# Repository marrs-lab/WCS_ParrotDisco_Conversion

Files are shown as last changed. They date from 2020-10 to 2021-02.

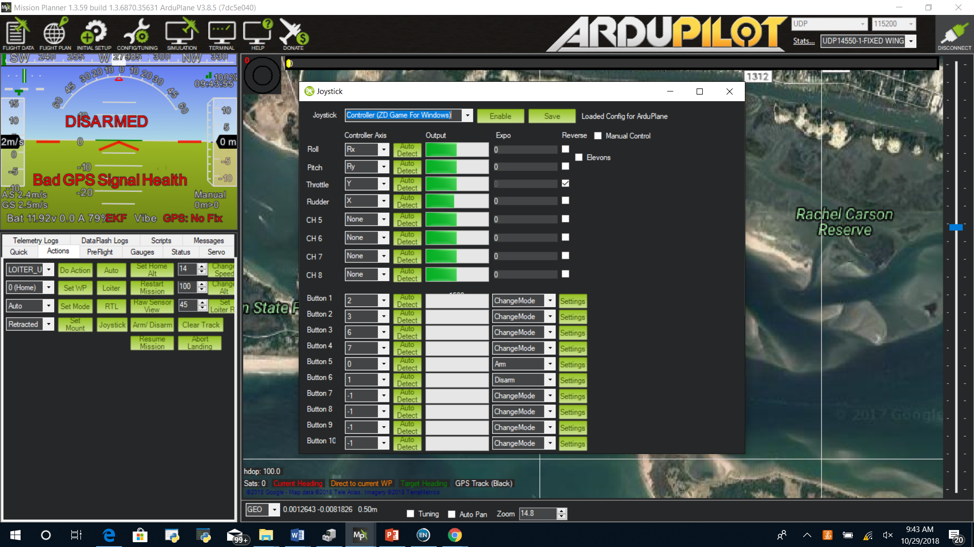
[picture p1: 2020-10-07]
Notes/Gamepad settings .png

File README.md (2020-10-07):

# WCS_ParrotDisco_Conversion

Before we begin, there are some important warnings…

**WARNING** 
Modifying the Parot Disco will void any warranties and could damage the aircraft. Only perform these modifications if you have adequate technical skills to 
perform the modifications.

**Disclaimer** 
The information provided by [Julian Dale or Duke University MaRRS Lab] (“we,” “us” or “our”) on [marineuas.net or Github/marrs-lab] (the “Site”) is for general informational purposes only. All information on the Site is provided in good faith, however we make no representation or warranty of any kind, express or implied, regarding the accuracy, adequacy, validity, reliability, availability or completeness of any information on the Site.

Under no circumstance shall we have any liability to you for any loss or damage of any kind incurred as a result of the use of the site or reliance on any information provided on the site. Your use of the site and your reliance on any information on the site is solely at your own risk. 

About the information included:

>

There are three folders containing ;

| Folder | Description |
| --- | --- |
| 3D Printer Files | STL's for printing the mouting frame |
| Autopilot files | The files required to transfer to the Parot Disco CHUCK autopilot to enable running Arduplane and on the autopilot for aircraft and external camera control and the parameters to set the aircraft up. |
| Manual | Manual for operating the aircraft and flight planning. Initial set up, calibrating sensors and installing Sony gamepad. Using external WiFi for extended range. Also notes on camera set up and modifying the parameters file for camera control using seagulUAV #MAP2 camera trigger |
| Notes | Information for converting the Disco to carry and trigger the Sony RX0 camera. Also manufacturing a 7000mAhr LiIon battery pack |
| QGroundControl | Links to most recent tested version of QGroundControl |

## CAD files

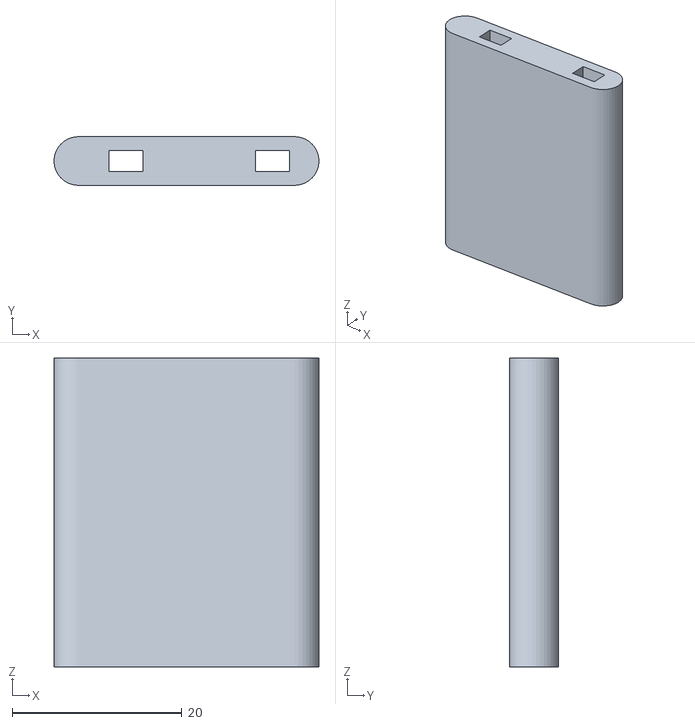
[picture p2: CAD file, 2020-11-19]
3D printer files/Dummy RX0 battery case v5.0.STL
31.2 x 5.75 x 36.4

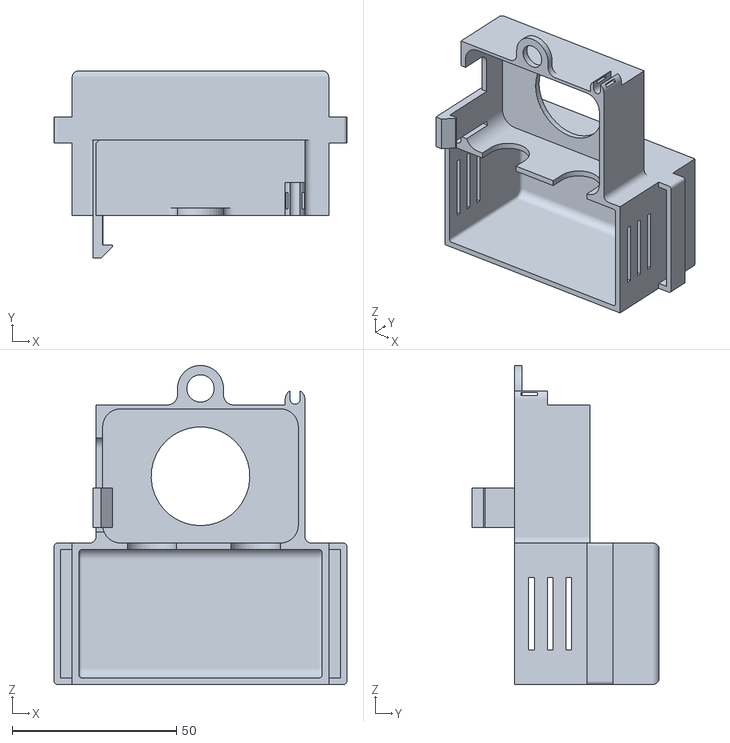
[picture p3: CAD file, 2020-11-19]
3D printer files/Disco RX0 mountv4.2STL.STL
89.0 x 57.0 x 97.0

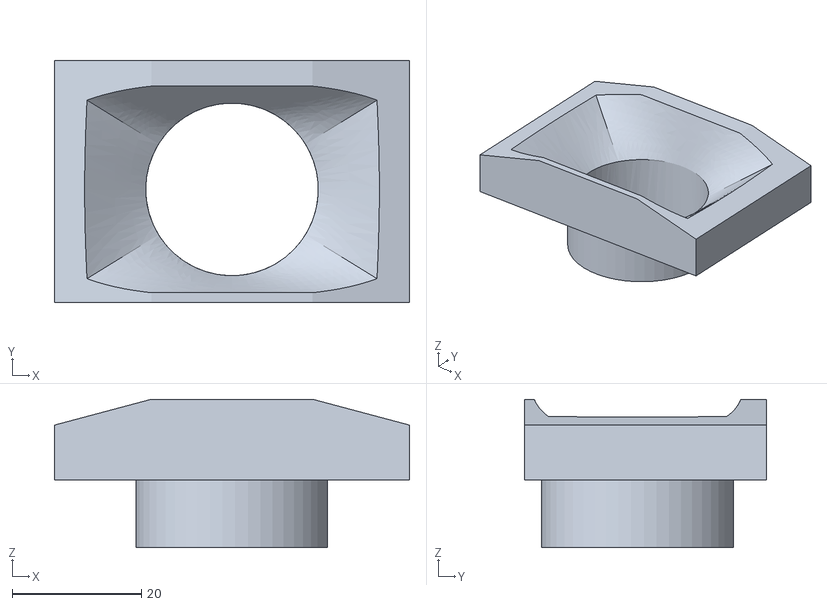
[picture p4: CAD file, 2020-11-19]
3D printer files/RX0 lens shield v2.0.STL
55.0 x 37.5 x 23.0

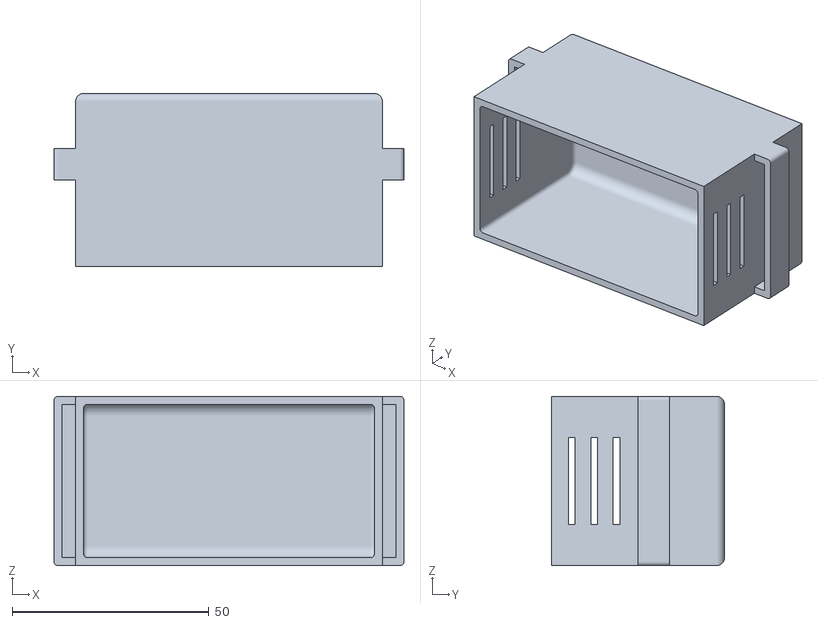
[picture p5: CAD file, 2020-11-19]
3D printer files/Disco 7000mahr battery tray.STL
89.0 x 44.0 x 43.0

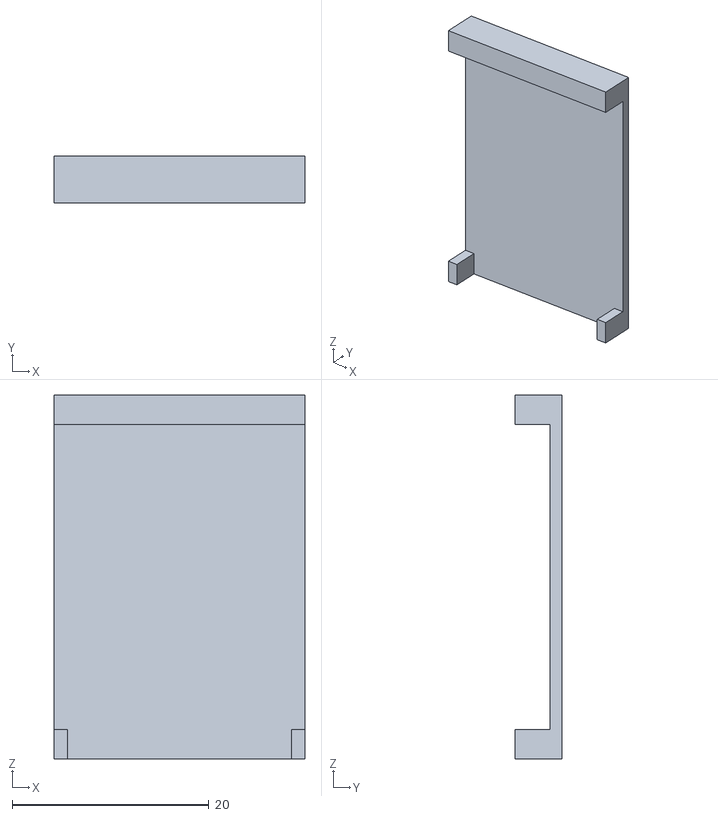
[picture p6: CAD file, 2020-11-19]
3D printer files/Dummy battery coverv2.0.STL
25.5 x 4.75 x 37.0

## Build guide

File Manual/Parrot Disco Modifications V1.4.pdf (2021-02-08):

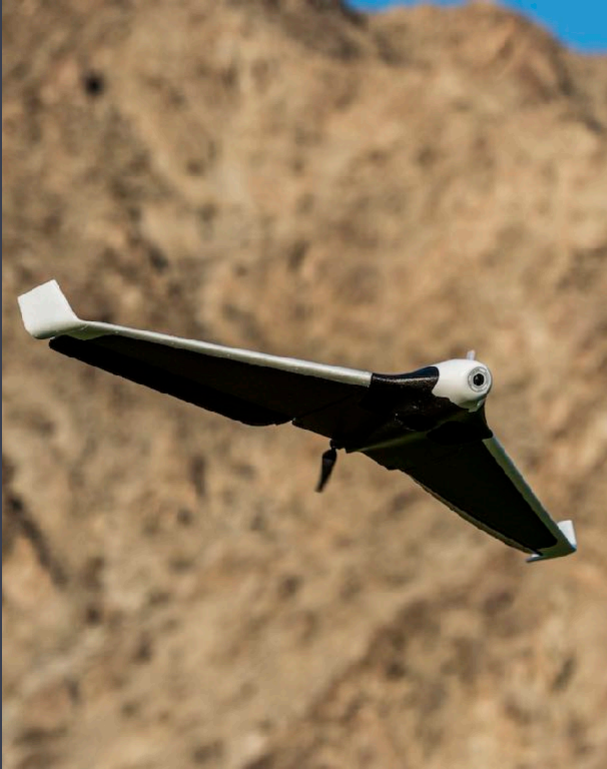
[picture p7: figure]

# Julian Dale

# THE PARROT DISCO

# MODIFIED

### Flight manual for conversion and operation

Version 1.4. 2021-02

## Background to the

# Modifications

- Load arduplane firmware on aircraft to allow flight planning capability
- Install downward facing RGB camera for mapping
- Setup PS4 wireless remote controller for manual flight
- Define parameters and mission planning protocols under
QGroundcontrol environment
- Provide data process to import images into Pix4D for analysis.

Although the Parrot disco is a very capable, easy to fly and inexpensive aircraft, it lacks the ability to fly mapping missions under the parrot Freeflight app environment. To be fair this aircraft was never initially intended for this type of operation. Parrot did however provide the architecture to allow the disco to fly under the open source ardupilot firmware.

The origins of this project were to create a very low cost mapping aircraft with extended flight time. The intent was to send this out to field teams within the WCS (Wildlife Conservation Society) network to provide them with mapping and inspection capabilities in order to help their conservation efforts.

# Overview

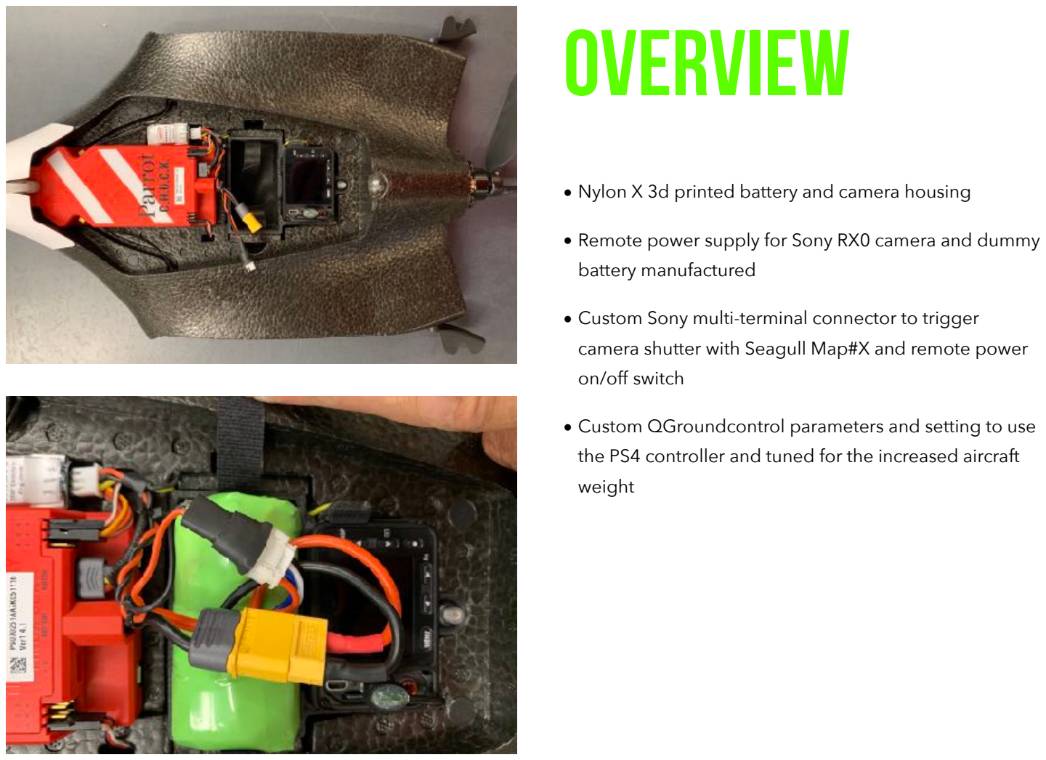
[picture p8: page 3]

- Nylon X 3d printed battery and camera housing
- Remote power supply for Sony RX0 camera and dummy battery manufactured
- Custom Sony multi-terminal connector to trigger camera shutter with Seagull Map#X and remote power on/off switch
- Custom QGroundcontrol parameters and setting to use the PS4 controller and tuned for the increased aircraft weight

# Contents

## 1. Installing the PS4 controller 2. Connecting the Disco 3. Configuring QGroundcontrol 4. Camera setup 5. Flight planning 6. Flight execution 7. Post flight data management 8. Maintenance

## Appendix A. Installing arduplane B. Load parameter file C. Camera specifications D. Airframe modifications E. Checklists: Pre-fight/maintenance F. Notes

# 1. Install PS4 controller

## DualShock 4 Bluetooth Pairing Settings

Step 1:
- To pair the DS4 with a computer, first put the controller into pairing mode by press and HOLDING the PlayStation button and Share button at the same time for 3 seconds. Hold these buttons until the light bar starts rapidly flashing.
Step 2:
- If your Operating System is Windows 7 then you have to right click on the Bluetooth Icon on the bottom right tray. If you are using Windows 8 or higher, open Bluetooth Settings by clicking on the Speech Bubble icon in the Task Bar on the bottom right corner.
- This will launch Action Center, click on Bluetooth and wait for the Wireless Controller to Appear.
- Click on it and type 0000 for typing the Pair Code.

That’s it, the controller is now connected wirelessly. In case you find issue with detecting the Wireless Controller after turning on Bluetooth, troubleshoot your PC Bluetooth adapter by updating drivers.

## USB Connection

- The controller can also be connected directly to the PC with a USB to USB micro cable. This plugs into the charge port on the front of the controller.

## Power up Disco

1. Install battery as shown.
2. Connect main battery lead (Yellow XT60 connector)
3. Press power button once (Pitot tube). Aircraft will start up. Wait for the long tone
4. Press power button 3 times in quick succession. This will boot the Disco into Arduplane and it will play a short tune as it boots up.

## WiFi connection

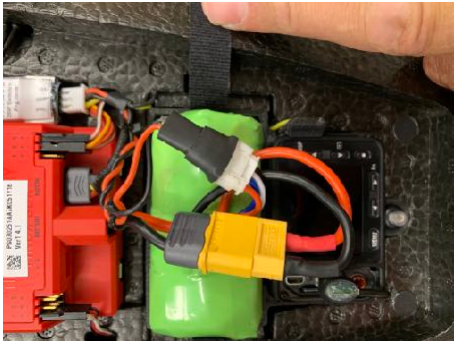
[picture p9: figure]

1. Use a long range USB WiFI modem such as the Alfa Long-Range Dual-Band AC1200 Wireless USB 3.0 Wi-Fi Adapter w/2x 5dBi External Antennas. You may need to download the latest driver for the Alfa USB WiFi modem here https://www.alfa.com.tw/download/all/1.htm (https://www.alfa.com.tw/download/all/1.htm)
2. Connect USB WiFi modem to the computer
3. Go to computer device manager and disable the computers inbuilt network adaptor or turn off the internal WiFi. *ensure you are only connecting to the aircraft using the long range WiFi modem and not your computers internal WiFi*
3. Connect to Disco WiFi from the computers network connection using the USB modem. Disco should appear as a DISCO-xxxxx as a WiFi connection **It is highly advised to disable all “connect automatically” options for your other WiFi connections. You do not want the aircraft to disconnect mid flight and have your computer connect to another network.**
4. Open QGroundcontrol. The Disco should connect automatically after a few seconds. If you encounter any issues. Shut down QGroundcontrol, ensure the disco is booted into Arduplane (three button presses on the pitot), the WiFi is connected to the aircraft then restart the app.

# 2. Connecting Disco

Getting QGroundControl up and running is quick and easy:
1. Download and install (https://docs.qgroundcontrol.com/en/getting_started/download_and_install.html) the application. Current stable version tested with the modified Disco is V4.0.10. Other versions many not function properly. You can go the the GitHub site to download previous versions. The link is on the downloads page for qGroungcontrol.
2. Start QGroundControl.
3. Attach your vehicle to the ground station device via USB, through a telemetry radio, or over WiFi. QGroundControl should detect your vehicle and connect to it automatically.
That's it! If the vehicle is ready to fly, QGroundControl should display Fly View (https://docs.qgroundcontrol.com/en/FlyView/FlyView.html) as shown below (otherwise it will open Setup View). (https://docs.qgroundcontrol.com/en/SetupView/SetupView.html)

# 3. Configuring QGroundcontrol

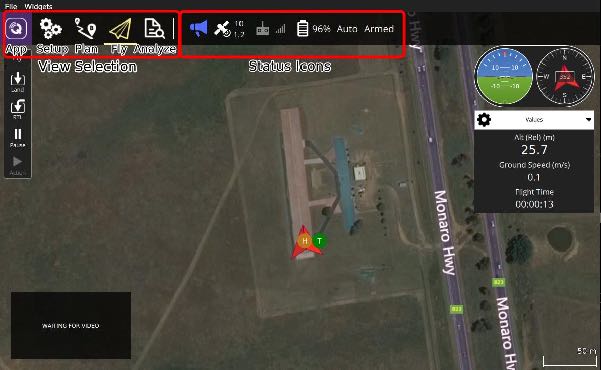
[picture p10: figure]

A good way to become familiar with QGroundControl is to start experimenting:

- Use the toolbar (https://docs.qgroundcontrol.com/en/toolbar/toolbar.html) to switch between the main views:
- Settings: (https://docs.qgroundcontrol.com/en/SettingsView/SettingsView.html) Configure the QGroundControl application.
- Setup: (https://docs.qgroundcontrol.com/en/SetupView/SetupView.html) Configure and tune your vehicle.
- Plan: (https://docs.qgroundcontrol.com/en/PlanView/PlanView.html) Create autonomous missions.
- Fly: (https://docs.qgroundcontrol.com/en/FlyView/FlyView.html) Monitor your vehicle(s) while flying.
- Click the Status icons on the toolbar to find out the status of the connected vehicle. While the UI is fairly intuitive, this documentation can also be referenced to find out more.

## Controller calibration

To configure a joystick:

1. Start QGroundControl and connect to a vehicle.
2. Connect the Joystick or Gamepad to a USB port or bluetooth.
3. Select the Gear icon (Vehicle Setup) in the top toolbar and then Joystick in the sidebar. The screen below will appear.
4. Make sure your joystick is selected in the Active joystick dropdown.
5. Press the Calibrate button and then follow the on-screen instructions to calibrate/move the sticks.
6. Test the buttons and sticks work as intended by pressing them, and viewing the result in the Axis/Button monitor.
7. Select the flight modes/vehicle functions activated by each joystick button. A maximum of 16 joystick button actions can be set.
8. Check the Enable joystick input checkbox to begin sending joystick commands to the vehicle.

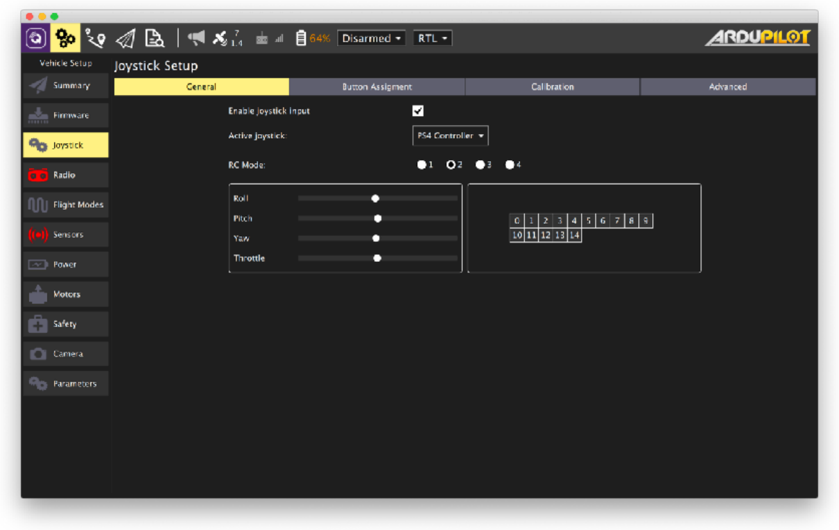
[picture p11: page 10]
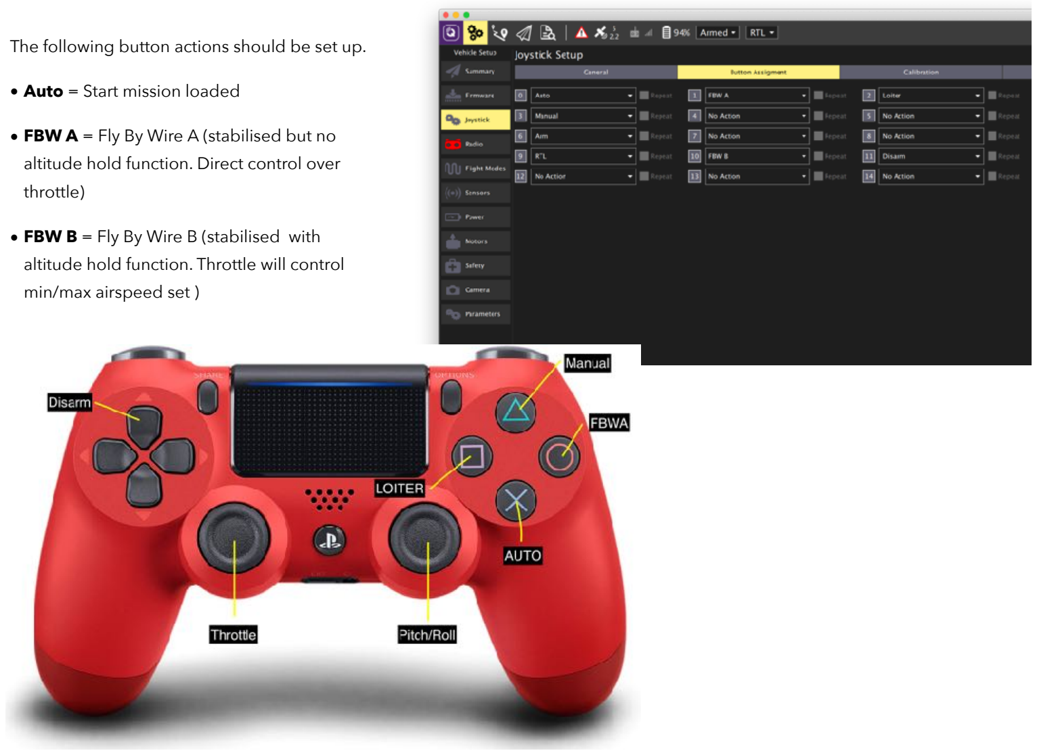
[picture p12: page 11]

The following button actions should be set up.

- Auto = Start mission loaded
- FBW A = Fly By Wire A (stabilised but no altitude hold function. Direct control over throttle)
- FBW B = Fly By Wire B (stabilised with altitude hold function. Throttle will control min/max airspeed set )

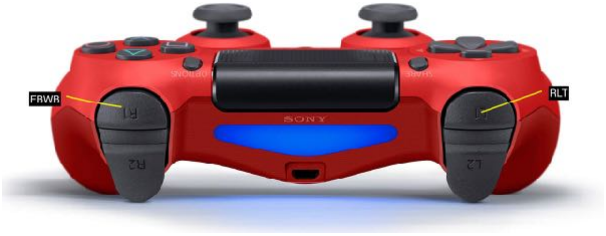
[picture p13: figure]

- Loiter = Will put aircraft into an orbit and maintain altitude
- Manual = Full manual control. NOT RECOMMENDED FOR FLIGHT. Use this mode only to verify flight controls on the ground.
- Arm = Arm the motor ready for takeoff
- Disarm = Disarm the motor
- RTL = Return to Launch. Aircraft will return to the home position and orbit.

## Sensor calibration

Perform the following calibrations as instructed

- Accelerometer
- Compass - Note. Ensure the battery cowling is fitted during compass calibration.
- Level Horizon = Using the level bubble measure on your phone. Sit the phone on the autopilot and lift the nose up by 3deg by placing something under the airframe. Ensure the wings are horizontal. When the aircraft is in the correct position and is completely still, hit the “level horizon” button
- Cal Baro/Airspeed = Cover the pitot tube with your had so it measure the static air pressure and is not influenced by the wind.

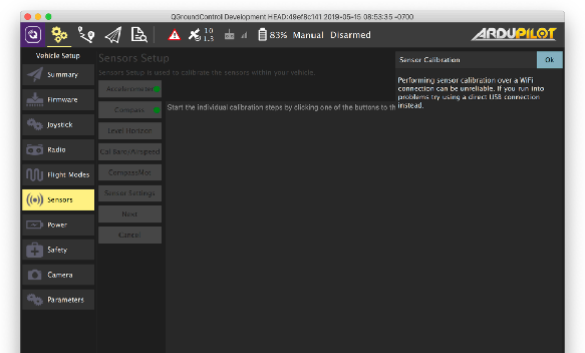
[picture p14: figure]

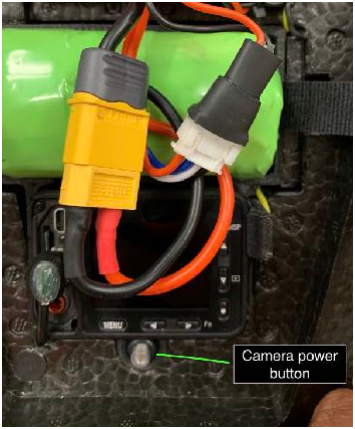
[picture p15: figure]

## Camera settings

Install the micro SD card.

Plug in the Sony Multi connector to the camera.

With the camera connected to the main flight battery, press the button below the camera to turn the camera on

A new or unformatted SD card will require a database to be set up before use. Power up the camera and hit “enter” at the image database creation prompt.

It is important to set the following camera parameters

1. Aspect ratio = 4:3
2. Manual shutter speed = 1/1250 is a good default speed
3. ISO = Auto
4. Focus = Wide
5. Set the camera time to GMT
6. Ensure the SD card has enough space

# 4. Camera setup

## Camera Parameters

| Width | Height
Sensor Size | 13.2mm | 8.8mm
Image px | 4272 | 3200
Focal length | 7.7mm

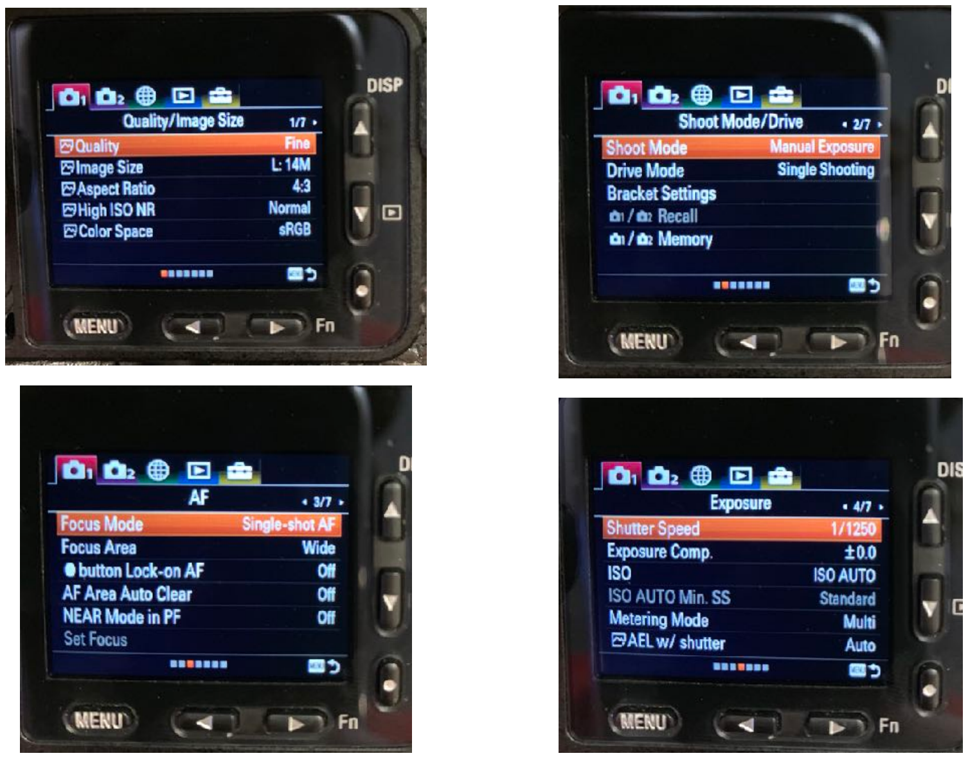
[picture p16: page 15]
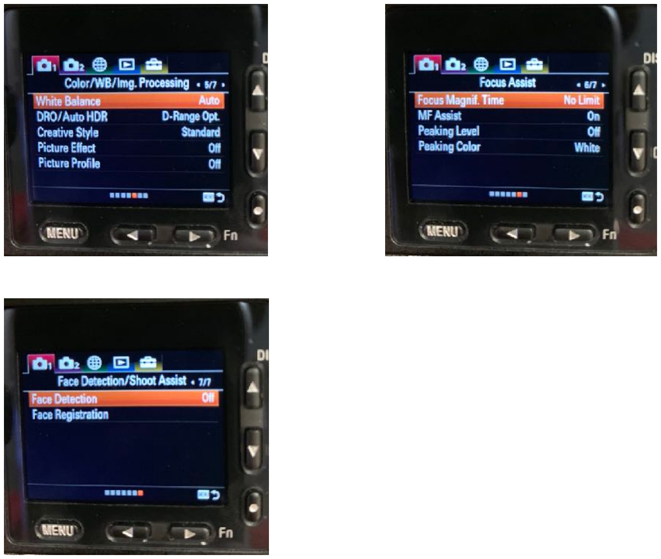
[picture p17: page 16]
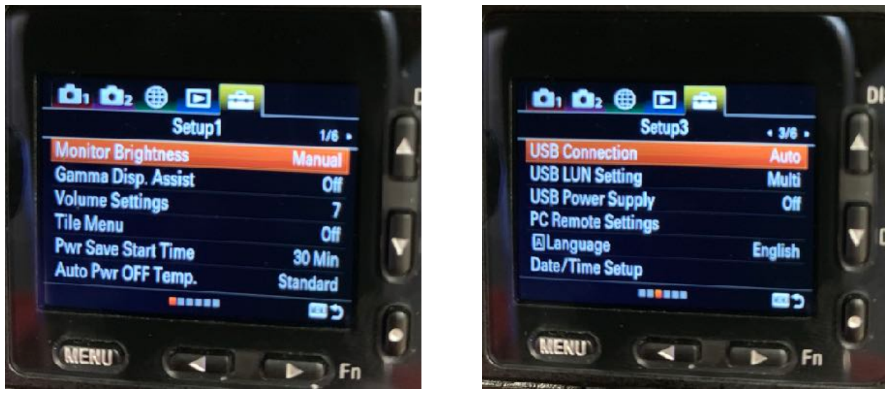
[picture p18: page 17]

# 5. Flight planning

## 1. Download base maps

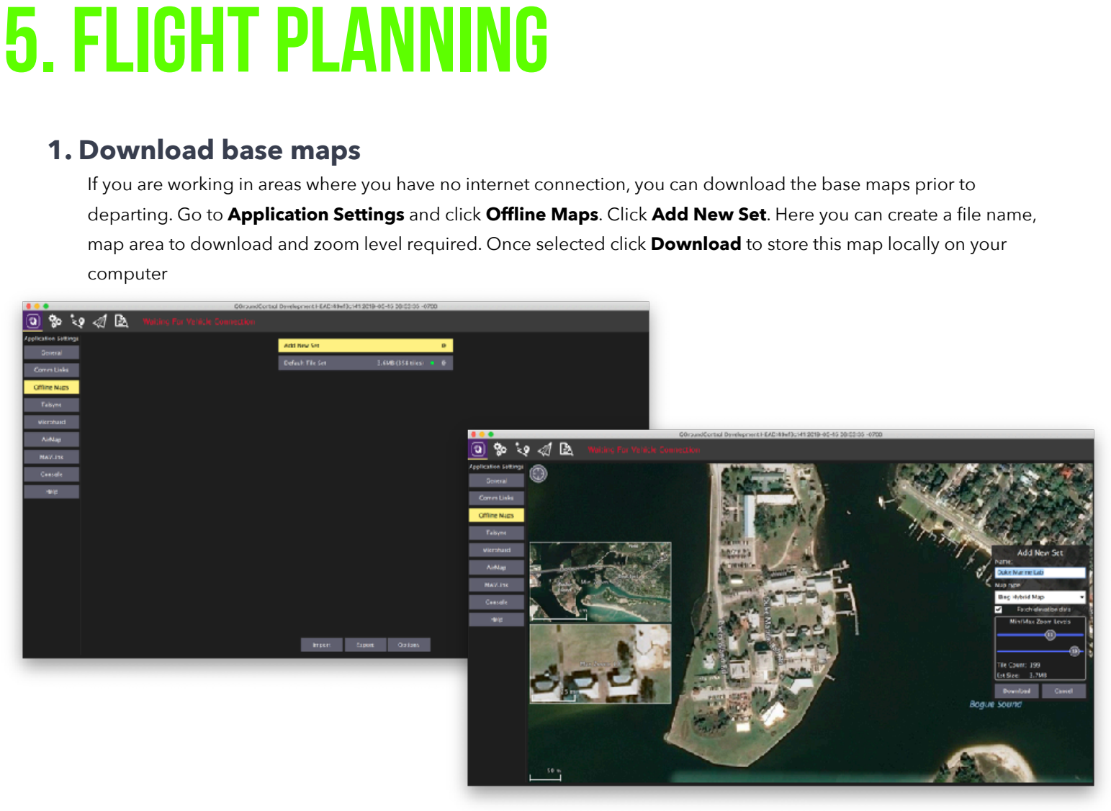
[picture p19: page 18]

If you are working in areas where you have no internet connection, you can download the base maps prior to departing. Go to Application Settings and click Offline Maps. Click Add New Set. Here you can create a file name, map area to download and zoom level required. Once selected click Download to store this map locally on your computer

## 2.Planning a Survey

1. Home position will be set automatically at the position the Disco is powered up.
2. Click on Takeoff and move the waypoint close to the takeoff location and at an altitude where it will clear all obstacles.
3. The takeoff parameters will automatically be set in position1 of the mission list. Set the altitude to a sufficient height to clear all obstacles at takeoff. Set the takeoff pitch angle to 25deg
4. Set a waypoint close to the takeoff and in a position where the aircraft has a good entry to the first survey waypoint. You may need to adjust the current set survey speed if the winds are strong. To change this you need to click the “gear” icon and then select the parameters tab. In the search window type “trim_arspd_cm” Set speed to 1500cm/s for light winds. 1700cm/s for moderate and 1900cm/s for strong winds ~18mph. This will be the survey flight speed used during the flight.
5. Set a Survey area up as desired. Additional grips around the polygon can be added by clicking on the + on the perimeter. Set the camera to the Sony RX0.
6. Select the desired GSD or Altitude , Overlap (70% is a safe default for mapping). Adjust the orientation as required for efficiency. In winds greatest than12mph it is advised to fly with a cross wind rather than a head and tail wind. For low altitudes, you may want to set the Fly alternate transects under the options so the aircraft isn’t making tight turns at the turnarounds. Set the Turnaround distance to 120m. This allows enough distance to execute the turn and approach the start of the next transect.

7. Set the landing position on the desired landing position. You can physically move the aircraft to the desired landing spot and then set the centre of the green landing box on the aircraft icon for better accuracy. Remember to set move the landing loiter position so the glide slope approach line is into the wind and avoids all obstacles. The Loiter Point Altitude should be set to avoid all obstacles. The glide slope should be set to 10deg or less. Lower glide slope angle will give higher landing accuracy in combination with the wind speed and wind direction relative to your approach direction.
8. NOTE: In the Windows version of QGroundcontrol you will need to un-check the “stop taking images” and “stop taking video” boxes at the bottom of the landing tab. The mission upload will fail otherwise.

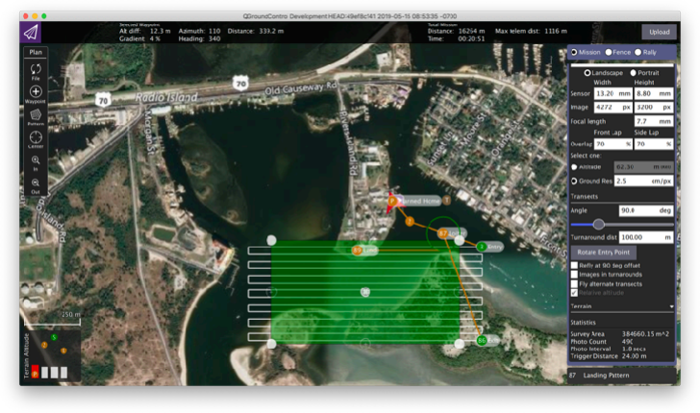
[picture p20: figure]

9. If flying in areas with elevation changes, you can enable the “Vehicle follows Terrain” option in the “Terrain” section of the survey. This uses a course digital terrain model from the satellite imagery to adjust the waypoints to allow for changes in elevation.

NOTE: This will not account for tall trees, antenna or other tall obstacles. Ensure you have sufficient altitude during all aspects of the takeoff, survey and landing to account fo these obstacles or elevation changes.

10. Once all the settings have be configured and verified. Click Upload

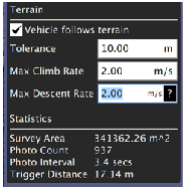
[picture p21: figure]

11. Before flight, go to the Safety (Fig Safety) settings and ensure the Return to Launch altitude is set appropriately for the surrounding environment and will clear any obstacles if a RTL failsafe is triggered. Note: the altitude is in CentiMeters
12. Click on the gear icon under the Head Up Display (Fig. Values) to add additional information to the values panel.
13. Click the triangle (fig. Camera) to switch to camera and with camera turned on click “trigger camera” to test.

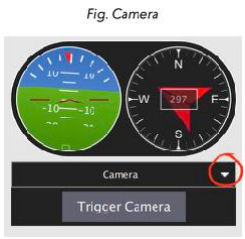
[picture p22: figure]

Fig. Safety | Fig. Values

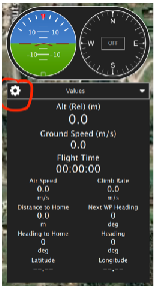
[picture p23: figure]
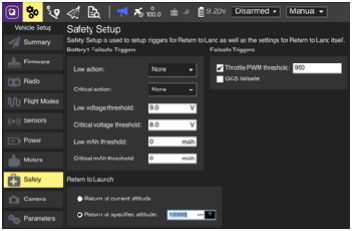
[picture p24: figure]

# 6. Flight Execution

1. Turn on the camera and check the lens is clean and there is an SD card installed
2. Perform the PRE-Flight check as per appendix E. Checklists
3. Go back to the flight page and verify the mission waypoints are displayed.
4. Check all telemetry data inc battery voltage, #GPS satellites. Check compass is stable and not drifting and artificial horizon corresponds to movement in vehicle attitude. Check airspeed sensor by blowing at the pitot tube front, gently.
5. Move the aircraft to the launch location and ensure the aircraft is pointing into the wind and the direction you wish to takeoff. This is important as this will be the direction that is set for the takeoff.
6. Using the Gamepad or clicking on the mode on the top of the screen, change the aircraft to manual mode. Move the joystick and verify the control surfaces are working and in the correct directions.
7. Slide the ARM button or select AUTO then ARM on the gamepad. The aircraft should beep and the aircraft mode should now show auto and armed.
8. Carefully pick up the aircraft. Hold each wing on the leading edge and keep arms and clothing clear of the propeller. Shake to wake up the aircraft. The motor will spool up to full throttle. Point the aircraft at a 30deg angle upward and into the wind. Take a step forward and push the aircraft up in this 30deg slope. Do not flick your wrists as this will cause the aircraft nose to go high and stall the aircraft.
9. The aircraft will climb to the takeoff altitude, then head for the first waypoint.
10. You can interrupt the mission at any time by clicking on the mode a the top of the screen and select a mode from the dropdown menu (Loiter, RTL (Return to Launch) and Auto are most common) . Alternatively you can change modes via the gamepad.

11. Carefully monitor the battery voltage and aircraft telemetry. Minimum battery voltage you should operate down to is 9.5v . The aircraft motor will shut down at 8.5v!!
12. At any time during the flight you can increase the throttle to gain higher airspeed in the event of strong wind gusts if the aircraft is not making enough “speed over ground”
12. On the landing approach, if required you can input roll and throttle to adjust the landing of the aircraft in auto mode. Alternatively you can take full control in FBWA mode.This will allow you land and have direct control over the throttle. You can lower this for decent and pull all the way back to cut the motor. Once landed, click
DISARM to stop the motor spooling up again when you release the throttle stick.

# Stopping the Auto mission

If required you can pause, loiter or take manual control of the aircraft at any point. To continue on the mission or to re fly part of the mission, simply click on the desired start waypoint, confirm it and then go back to “Auto” mode

# Modifying the Flight plan in flight

If required the flight plan can be modified while the aircraft is airborne.

1. Put the aircraft in a “Loiter”
2. Make the changes to the flight plan in the “planning” tab and upload when satisfied.
3. Click on the desired start waypoint and “confirm”.

# 7. Post Flight data management

1. Disarm the aircraft and leave powered on.
2. Go to the Analyse tab and click Refresh
3. Select the last log from the folder. It should contain the date and time of the last flight. Create a folder on the computer with reference to the flight/location/time etc as desired.
4. Download the flight log to that folder.
5. Remove the SD card from the camera and copy the images from the flight to the same folder.
6. Backup the data on a separate hard drive.
7. Erase the images from the SD card when backup completed.
8. You can erase the logs stored on the autopilot to make it easier to associate the correct log with the images. Unfortunately the log files lose their date&time information when the aircraft is powered back up.
9. Ensure you disconnect the battery at the connector when finished. The switching regulator powering the Sony camera will continue to drain the battery if still connected and may destroy the battery if over discharged.

# 8. Maintenance

It is important to perform Preflight inspections prior to each flight. This should pick up any faults and avoid having an in air incident.

We recommend a full aircraft inspection every 10 flight hours.

This should include

1. Close inspection of all wing connections and hinges
2. Airframe damage and skid plate secure. Check for delimitation in the airframe at the joints.
3. Pitot tube is clear
4. Servo operation through the full range of movement.
5. Motor rubber mounts are in good conditions and the bolts are snug
6. Propellers are free from damage and the mounting bolts are tight.
7. Motor spins freely and no contamination present.
8. Check all wiring for signs of chaffing or damage.

# APPENDIX

# A. Install Arduplane

The following information is for installing ArduPlane on the Disco for the first time.

Please Note: The current stable firmware version tested on this project is

Arduplane Disco FW = v 3.9.8.

Parrot Disco FW (installed through the Parrot Freeflight app) = v 1.7.1

For flight operations only! = QGround Control v 4.0.10

***** When uploading the parameters file it is critical you use QGroundcontrol v3.5.6 which was the last stable release before v 4+…. Using version 4+ will result in the parameters loading correctly and potentially some serious flight characteristics. We have not encountered any issues flying the aircraft under version QGroundControl v 4+ but strange behaviours when trying to load parameters under the later versions.****

Build files, manuals and all the latest firmware and parameters can be found at

https://github.com/marrs-lab/WCS_ParrotDisco_Conversion

- Download FileZilla from https://filezilla-project.org
- Install and set transfer type to “binary”
- Install battery in Disco and start by pressing on the pitot tube.
- After start up go to the computer wifi network and select “DISCO-xxxxxx” (the xxxxx will be the serial number of the Disco.
- Once connected, go back to Filezilla and enter 192.168.42.1 as the host: Click connect.
- Navigate to the /internal_000/ardupilot folder in the right hand window (remote site)

# A. Installing ArduPlane

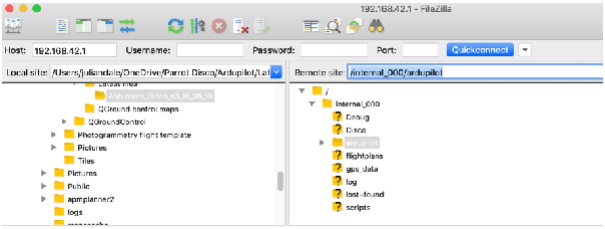
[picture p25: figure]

- Navigate to the files provided* in the left hand file browser and copy the files provided into the /ardupilot folder.
- You should have the following files in the /ardupilot folder (the ArduPlane.stg file and logs+terrain folders will populate as we configure the Disco in QGroundcontrol)

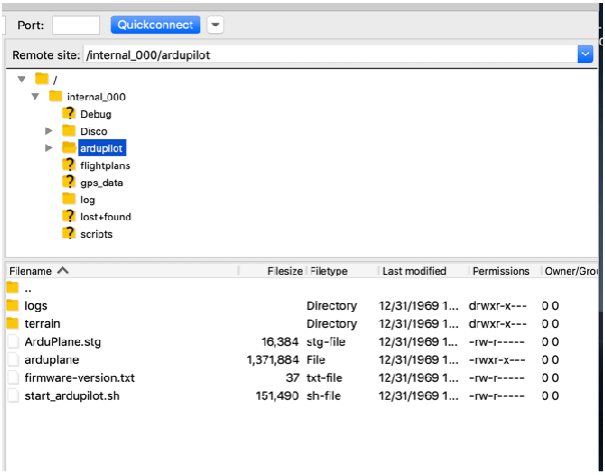
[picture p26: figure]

- arduplane
- Firmware-version.txt
- start_ardupilot.sh

# B. Installing Parameters file

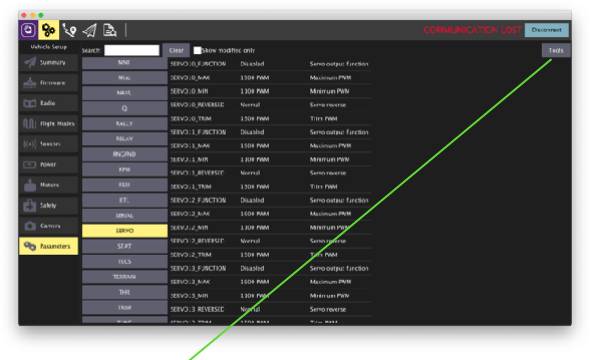
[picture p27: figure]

- Open QGroundControl v 3.5.6 and connect to the aircraft wifi
- Click on the Gear icon and then Parameters.
- Click the Tools button and select “Load from file”
- Load the .prams file dowloaded from the https://github.com/marrs-lab/WCS_ParrotDisco_Conversion
- Restart the aircraft and check the parameters.

# C. Camera specifications

# D. Airframe Modifications

Modified Disco Pre-flight checklist Checklist

Disco test flight (2019-07-13 12:00:00)

Passed | Not-passed Not-applicable
1 | Check airframe for signs of damage
2 | Check aircraft motors are mounted securely and check props for cracks and tightness
3 | Check area of operation for obstructions, people, and property
4 | Check payload is installed, connected, and secure
5 | Check pitot tube is clear
6 | Check wings are installed securely
7 | Check wings and alerions are in good condition and hinge mechanism are not damaged
8 | Check battery condition and install
9 | Lens clean
10 | SD card/memory installed with sufficient space available
11 | Power up aircraft
12 | Boot into Arduplane (press power switch 3 times)
13 | Connect modem
14 | Check AV Health. Battery
15 | Check AV Health. GPS satellites
16 | Check GCS battery level
17 | Verify fail-safes settings are appropriate for mission
18 | Upload flight plan to aircraft

Notes:

Full Name:
Phone:
Email:

# E. Checklists

# F. Notes

Servo rail pin numbers in the list below are from left to right when looking at the C.H.U.C.K from the back, so pin1 on the servo rail is closest to the first ‘C’ in ‘C.H.U.C.K’ on the case.
- channel 1 : servo rail pin 1
- channel 2 : servo rail pin 6
- channel 3 : I2C ESC motor output
- channel 4 : servo rail pin 2
- channel 5 : servo rail pin 5
- channel 6 : servo rail pin 3
- channel 7 : servo rail pin 4

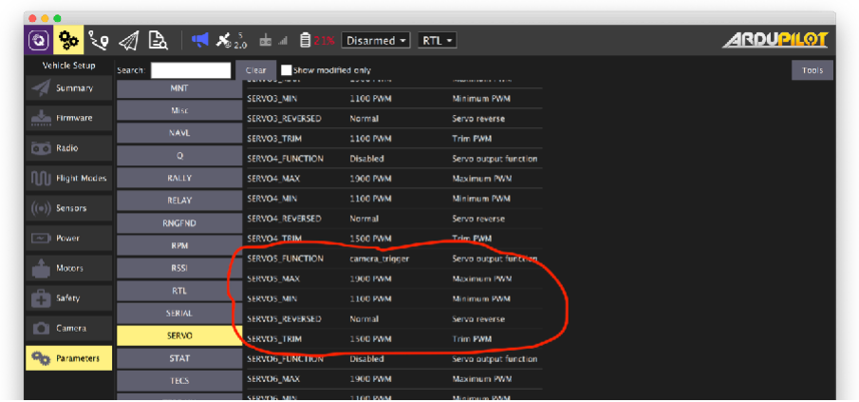
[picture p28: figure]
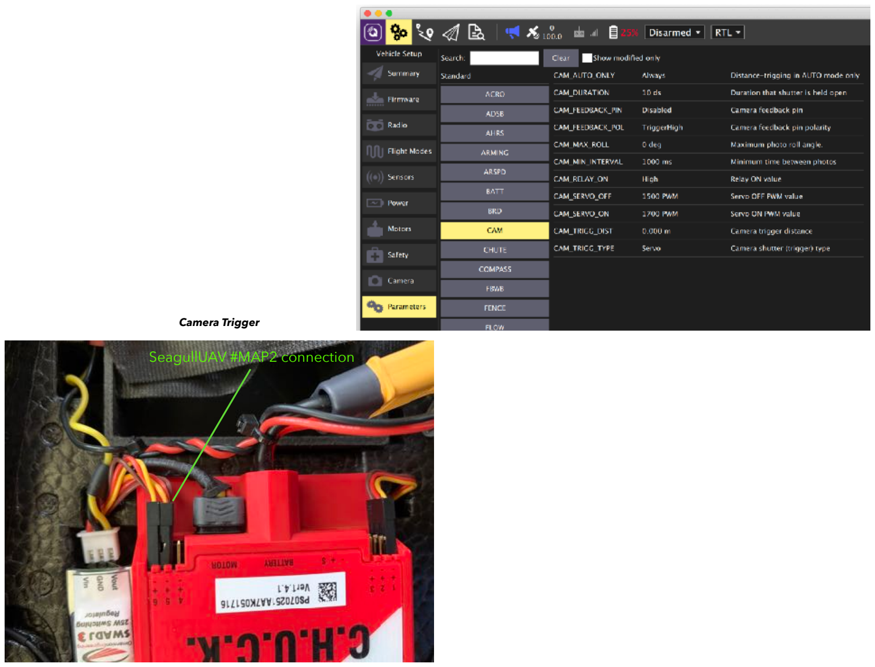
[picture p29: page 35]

SeagullUAV #MAP2 connection

Camera Trigger

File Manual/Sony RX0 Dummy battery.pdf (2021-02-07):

## Sony RX0 Dummy Battery

Parts required
- 3D printed battery case (ABS)
- 26 AWG silicon wire (red, yellow? and black. I have used yellow to distinguish between the 4V dc and the battery voltage)
- JST connector
- DimensionEngineering SWADJ3 adjustable voltage regulator https://www.dimensionengineering.com/products/de-swadj3
- Female JST-XH connector for connections to Lipo Balance lead.
- 3Pin JST-XH to connect to voltage regulator
- 100kΩ Resistor
- Copper/brass sheet.
- Superglue
- Hot Glue

Instructions.

1. Print 3d case and cover in ABS. Set at 100%infill
2. Cut small brass/copper sheet into squares that fit inside the battery case recesses.
3. Solder a yellow 100mm long copper wire cable to the positive terminal copper pad.
4. Solder a black 100mm long copper wire to the ground pad along with one leg of the 100kohm resistor. The legs may need to be trimmed shorter
5. Solder the other leg of the 100kohm resistor to the remaining centre pad.
6. Install the pads into the dummy battery housing, ensure the contacts and resistor are not shorting and use liberally squirt hot glue to hold in place.
7. Install the male JST connector on the power leads.
8. Install dummy battery cover and secure with a few drops of super glue
9. Cut 2 x 100mm silicon wires (black and red) Solder the wires to the GND pin and the opposite Voltage pins on the JST-XH connector. This will give you full battery voltage across all cells.
10. Solder both black GND wires (from the battery and the dummy camera connector) to the GND pin on the 3 pin male JST-XH connector
11. Solder the red battery cable to the corresponding Vin pin on the 3 pin male JST-XH connector
12. Solder the yellow wire from the dummy battery connector to the Vout pin on the 3 pin male JST-XH connector
13. Plug the voltage regulator into the battery, but leave the dummy battery disconnected and using a multimeter at the red JST connector, turn the pot to adjust the output voltage to 4V. Also check the polarity.

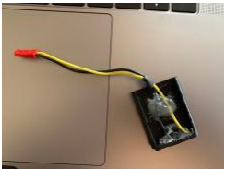
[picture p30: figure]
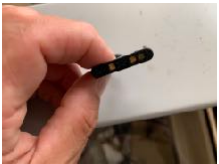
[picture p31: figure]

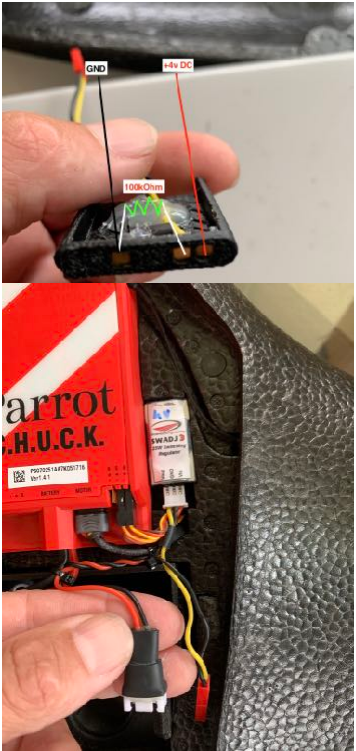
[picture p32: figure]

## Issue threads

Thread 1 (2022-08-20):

I could not disarm arduplane on parrot disco after installation arduplane from your manual.

hsy77101, 2022-08-20:
Thank you for your valuable data.
I tried to do after reading your manual.
But it didn't work properly.

Parrot Disco FW (installed through the Parrot Freeflight app) = v 1.7.1

The following is my procedure.
1. Turn on disco, and then connected pc wifi to wifi of parrot disco.
2. I copied your ardupilot files (WCS_ParrotDisco_Conversion-master\Autopilot files\Latest Arduplane FW)
    to "/internal_000" of parrot disco chuck using Filezilla.
4. Power off parrot disco and then Power on parrot disco.
5. Using Qgroundcontrol v3.5.6 , I connected parrot disco.
6. I upload \WCS_ParrotDisco_Conversion-master\Autopilot files\Latest ParameterFinal_FW3.9.8_210206.params
   to parrot disco by tool of Qgroundcontrol v3.5.6.
7. I could see fail message of writing parameter on Qgroundcontrol.
8. But I could not see all of parameter after copying ardupilot file to parro disco chuck.
9. And I could not disarm parrot disco. and I could not find parameter on qgroundcontrol  v3.5.6.

10. Power off , Power on and Clicking power button on Disco Three time
11. I could not also disarm parrot disco. and I could not find parameter on qgroundcontrol.

How can I solve it?

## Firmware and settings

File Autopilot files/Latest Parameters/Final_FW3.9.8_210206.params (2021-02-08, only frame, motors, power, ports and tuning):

1	1	BATT2_MONITOR	0	2
1	1	BATT_AMP_OFFSET	0.000000000000000000	9
1	1	BATT_AMP_PERVLT	17.000000000000000000	9
1	1	BATT_CAPACITY	0	6
1	1	BATT_CRT_MAH	0.000000000000000000	9
1	1	BATT_CRT_VOLT	8.500000000000000000	9
1	1	BATT_CURR_PIN	-1	2
1	1	BATT_FS_CRT_ACT	2	2
1	1	BATT_FS_LOW_ACT	1	2
1	1	BATT_FS_VOLTSRC	0	2
1	1	BATT_LOW_MAH	0.000000000000000000	9
1	1	BATT_LOW_TIMER	10	2
1	1	BATT_LOW_VOLT	9.500000000000000000	9
1	1	BATT_MONITOR	6	2
1	1	BATT_SERIAL_NUM	-1	6
1	1	BATT_VOLT_MULT	10.950758934020996094	9
1	1	BATT_VOLT_PIN	-1	2
1	1	BATT_WATT_MAX	0	4
1	1	FLTMODE1	0	2
1	1	FLTMODE2	11	2
1	1	FLTMODE3	11	2
1	1	FLTMODE4	6	2
1	1	FLTMODE5	11	2
1	1	FLTMODE6	10	2
1	1	FLTMODE_CH	5	2
1	1	INS_GYRO_FILTER	5	2
1	1	SERIAL0_BAUD	115	6
1	1	SERIAL0_PROTOCOL	2	2
1	1	SERIAL1_BAUD	57	6
1	1	SERIAL1_PROTOCOL	1	2
1	1	SERIAL2_BAUD	57	6
1	1	SERIAL2_PROTOCOL	1	2
1	1	SERIAL3_BAUD	38	6
1	1	SERIAL3_PROTOCOL	5	2
1	1	SERIAL4_BAUD	38	6
1	1	SERIAL4_PROTOCOL	5	2
1	1	SERIAL5_BAUD	57	6
1	1	SERIAL5_PROTOCOL	-1	2
1	1	SERIAL6_BAUD	57	6
1	1	SERIAL6_PROTOCOL	-1	2
1	1	SERVO1_FUNCTION	77	2
1	1	SERVO1_MAX	2000	4
1	1	SERVO1_MIN	1000	4
1	1	SERVO1_REVERSED	0	2
1	1	SERVO1_TRIM	1561	4
1	1	SERVO2_FUNCTION	78	2
1	1	SERVO2_MAX	2000	4
1	1	SERVO2_MIN	1000	4
1	1	SERVO2_REVERSED	1	2
1	1	SERVO2_TRIM	1576	4
1	1	SERVO3_FUNCTION	70	2
1	1	SERVO3_MAX	1900	4
1	1	SERVO3_MIN	1100	4
1	1	SERVO3_REVERSED	0	2
1	1	SERVO3_TRIM	1100	4
1	1	SERVO4_FUNCTION	0	2
1	1	SERVO4_MAX	1900	4
1	1	SERVO4_MIN	1100	4
1	1	SERVO4_REVERSED	0	2
1	1	SERVO4_TRIM	1500	4
1	1	SERVO5_FUNCTION	10	2
1	1	SERVO5_MAX	1900	4
1	1	SERVO5_MIN	1100	4
1	1	SERVO5_REVERSED	0	2
1	1	SERVO5_TRIM	1500	4
1	1	SERVO6_FUNCTION	0	2
1	1	SERVO6_MAX	1900	4
1	1	SERVO6_MIN	1100	4
1	1	SERVO6_REVERSED	0	2
1	1	SERVO6_TRIM	1500	4
1	1	SERVO7_FUNCTION	0	2
1	1	SERVO7_MAX	1900	4
1	1	SERVO7_MIN	1100	4
1	1	SERVO7_REVERSED	0	2
1	1	SERVO7_TRIM	1500	4
1	1	SERVO8_FUNCTION	0	2
1	1	SERVO8_MAX	1900	4
1	1	SERVO8_MIN	1100	4
1	1	SERVO8_REVERSED	0	2
1	1	SERVO8_TRIM	1500	4
1	1	SERVO9_FUNCTION	0	2
1	1	SERVO9_MAX	1900	4
1	1	SERVO9_MIN	1100	4
1	1	SERVO9_REVERSED	0	2
1	1	SERVO9_TRIM	1500	4

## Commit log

2020-10-07 Initial upload
    [Disco_Params_091820.params, Fixedwing_default.param, Inferno_arduplanev1.2_camSV07CH4.param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]
2020-10-07 Reorg of files and add readme
    [Disco_Params_091820.params, Fixedwing_default.param, Inferno_arduplanev1.2_camSV07CH4.param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]
2020-11-19 added params files
    [Disco 7000mahr battery tray.STL, Disco RX0 mountv4.2STL.STL, Dummy RX0 battery case v5.0.STL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]
2020-11-20 Updated params
    [WCS_Disco_upgrade_11_2020_v4.0.params]
2021-01-06 Update
    Updated manual and revised parameters after autotue failure.
    Reduced WP-radius values to try and follow tracklines closer
    [WCS_Disco_upgrade_01_2021_v1.0.params, WCS_Disco_upgrade_11_2020_v4.1.params, WCS_Disco_upgrade_11_2020_v4.2.params]
2021-01-11 Added original param file
    [Inferno_arduplanev1.5_2018_12_18.param]
2021-01-11 added folders
    added various disco paramteters folder to tack individual aircraft changes/settings
    [Latest_2021_01_11.params]
2021-01-19 Updated tuning params
    [Latest_2021_01_13.params, Latest_2021_01_13V1.0_Pretune.params, Latest_2021_01_13V1.1_Final_tune of ptch_rll.params]
2021-01-19 landing tuning
    [Latest_2021_01_19_land_params tuningv1.0.params, Latest_2021_01_19_postflighttuning.params]
2021-02-07 Final testing params
    [Final_2021_01_22.params, Final_FW3.9.8_210206.params, Latest_2021_01_22.params]
2021-02-07 work laptop sync
    [Final_v3.5.6_01022021.params, Final_v3.5.6_26012021.params, Latest_2021_01_11.params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]
2021-02-07 File cleanup
    [Disco_Params_091820.params, Final_2021_01_22.params, Final_FW3.9.8_210206.params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]
2021-02-08 Updated manual
    [Final_FW3.9.8_210206.params]
